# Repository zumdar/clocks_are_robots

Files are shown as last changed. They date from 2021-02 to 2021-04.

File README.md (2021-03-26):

# clocks_are_robots
## ECE3872 musical robot team 5B 

Tinkercad Simulation of Arduino and circuity: <br>
https://www.tinkercad.com/things/kZ8lBtSx1vj-copy-of-ece3872-time-zeeper/editel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

**Arduino Pinouts**

A0 - Audio in <br>
A1 - Enveloped audio in<br>
A2 - Octave knob <br>
<br><br>
[D4 - D7] are for stepper motor<br>
D4 - AIn1<br>
D5 - Ain2<br>
D6 - Bin1<br>
D7 - Bin2<br>
D8 - Start/Stop Button<br>
D9 - Tone out <br>
D10 - Servo out<br>
D12 - Neopixel LED out<br>

# glamour shots

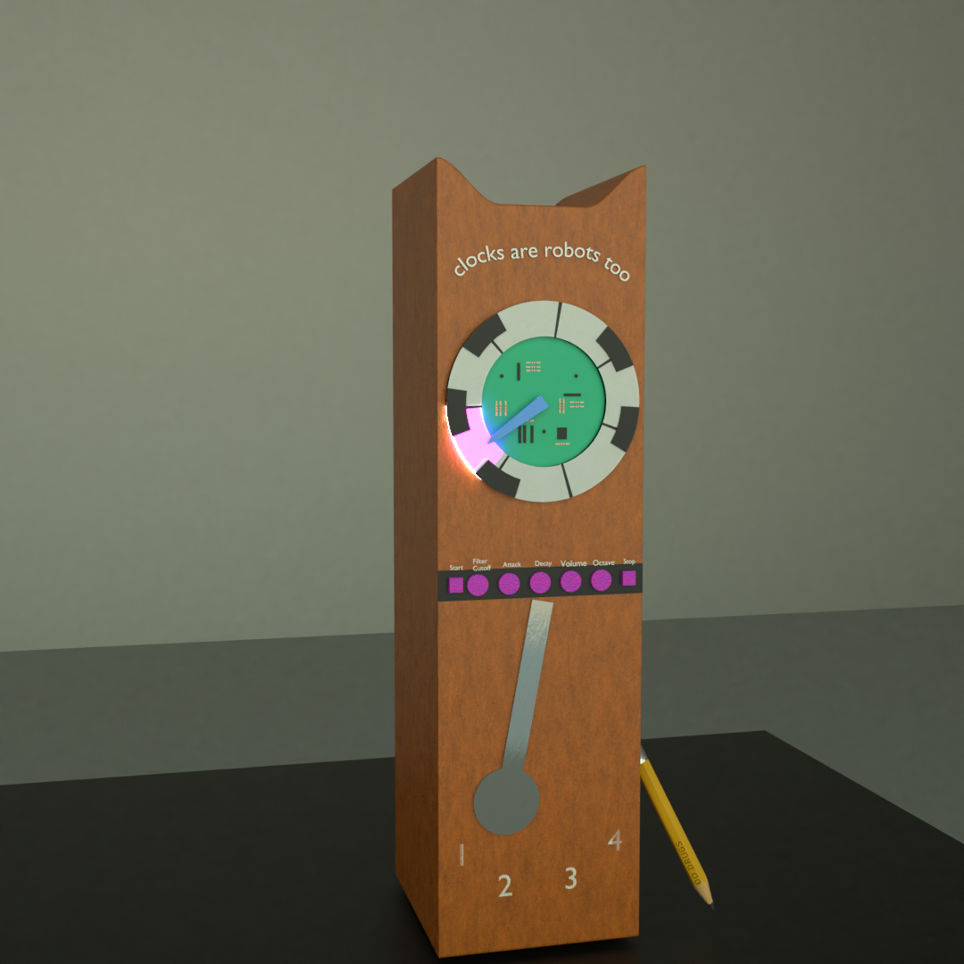
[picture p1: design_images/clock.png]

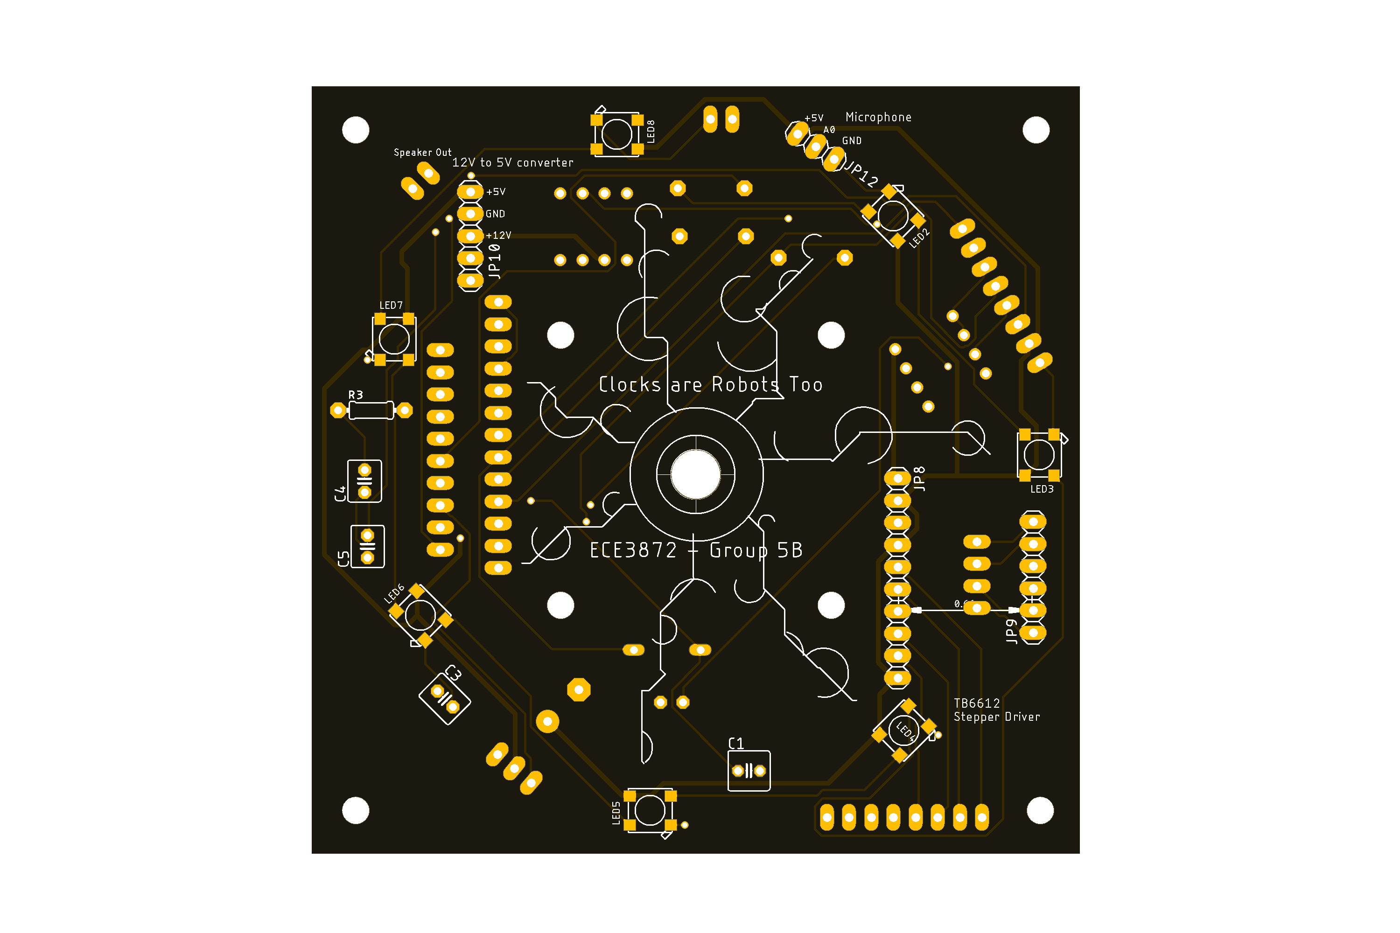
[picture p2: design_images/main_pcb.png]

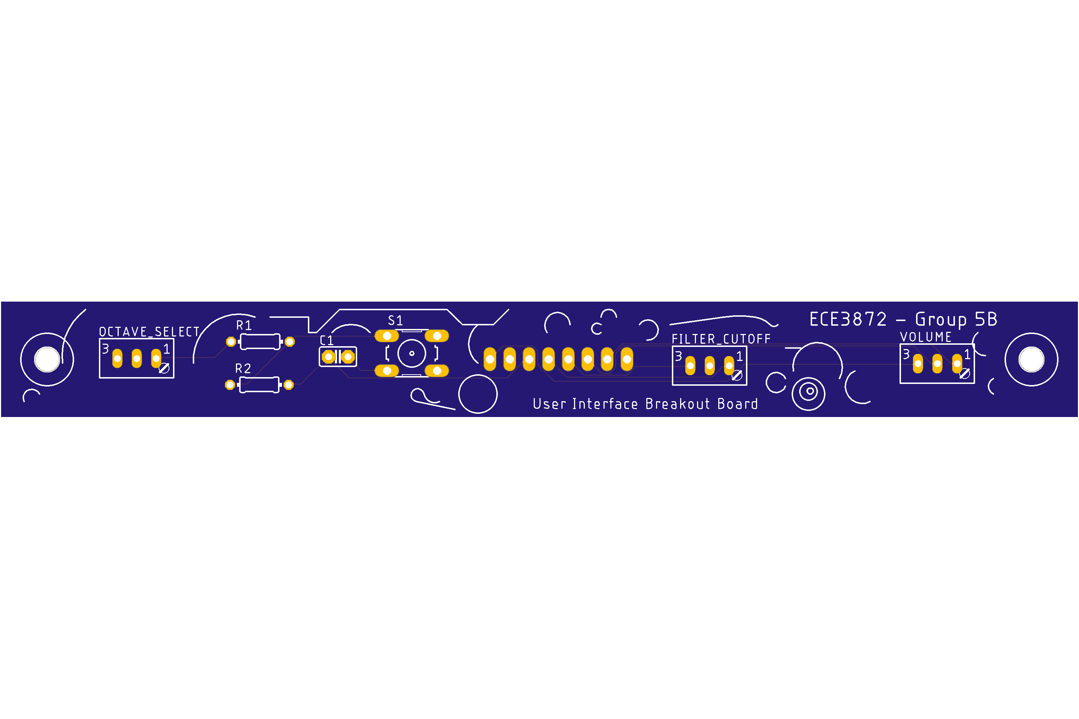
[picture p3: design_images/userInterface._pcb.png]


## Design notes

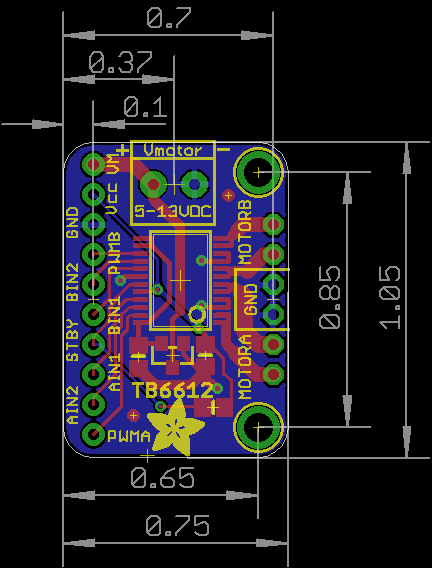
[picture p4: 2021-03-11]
schematics and PCBs/Main_Schematic_and_PCB/StepperMotorDriver_footprint.png

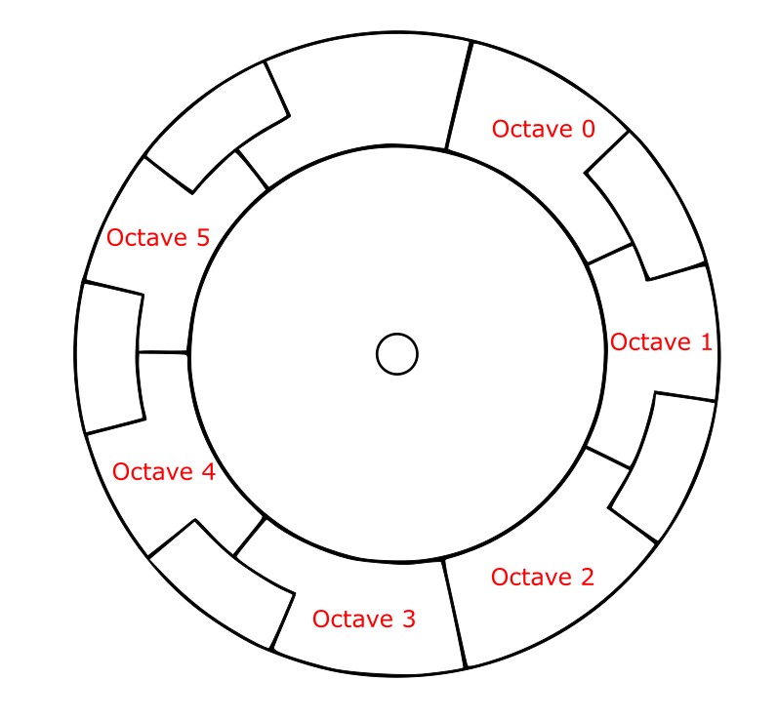
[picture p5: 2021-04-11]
physical_design_files/Annotation 2021-04-11 151619.jpg

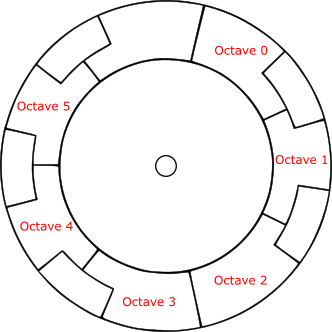
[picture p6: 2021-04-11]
physical_design_files/path1035.png

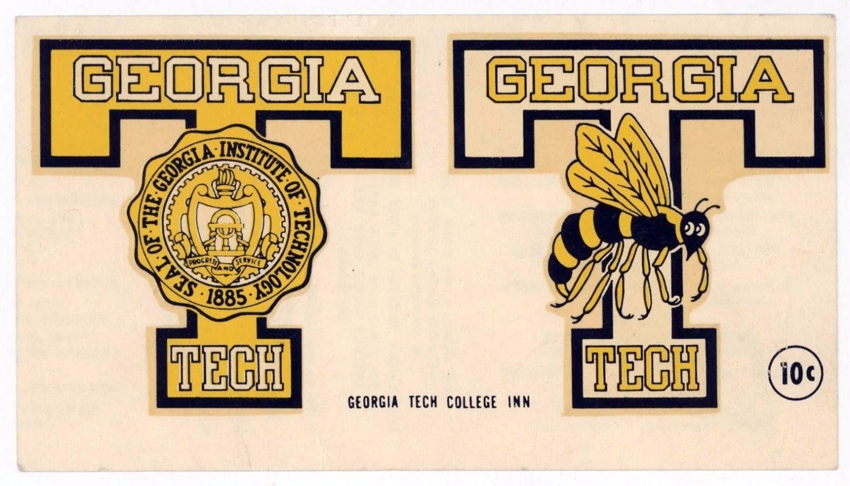
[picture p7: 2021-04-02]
physical_design_files/full clock svgs/f85bab5458ab0abd7dc41fa806446cff.jpg

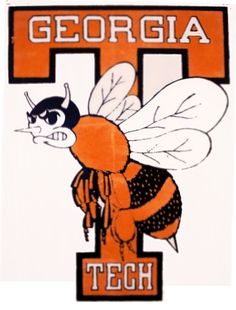
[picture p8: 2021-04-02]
physical_design_files/full clock svgs/cf619c819b96847c2e3a3e8340d46b5b--georgia-decals.jpg

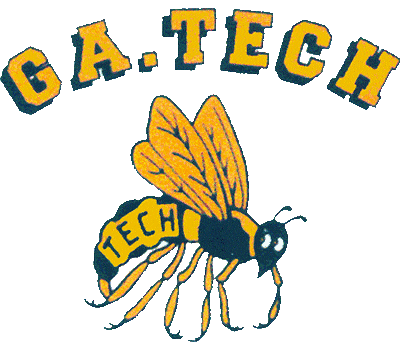
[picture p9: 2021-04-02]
physical_design_files/full clock svgs/d8595733d2d420681d40a56e9d078326.gif

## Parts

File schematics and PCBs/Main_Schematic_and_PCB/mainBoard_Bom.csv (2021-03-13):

Qty | Value | Device | Package | Parts | Description
2 |  | PINHD-1X10 | 1X10 | JP2, JP8 | PIN HEADER
1 |  | PINHD-1X13 | 1X13 | JP1 | PIN HEADER
2 |  | PINHD-1X2 | 1X02 | JP3, JP5 | PIN HEADER
2 |  | PINHD-1X3 | 1X03 | JP7, JP12 | PIN HEADER
1 |  | PINHD-1X4 | 1X04 | JP11 | PIN HEADER
1 |  | PINHD-1X5 | 1X05 | JP10 | PIN HEADER
1 |  | PINHD-1X6 | 1X06 | JP9 | PIN HEADER
2 |  | PINHD-1X8 | 1X08 | JP4, JP6 | PIN HEADER
1 | .05uF | C-US025-040X050 | C025-040X050 | C4 | CAPACITOR, American symbol
1 | 10 | R-US_0204/7 | 0204/7 | R3 | RESISTOR, American symbol
1 | 100 | R-US_0204/7 | 0204/7 | R1 | RESISTOR, American symbol
1 | 1000uF | CPOL-USE5-8.5 | E5-8,5 | C6 | POLARIZED CAPACITOR, American symbol
1 | 100nF | C-US025-040X050 | C025-040X050 | C3 | CAPACITOR, American symbol
1 | 1N4148DO35-7 | 1N4148DO35-7 | DO35-7 | D1 | DIODE
1 | 1k | R-US_0204/7 | 0204/7 | R2 | RESISTOR, American symbol
1 | 1uF | C-US025-040X050 | C025-040X050 | C2 | CAPACITOR, American symbol
1 | 1uF | C-US025-050X050 | C025-050X050 | C1 | CAPACITOR, American symbol
1 | 250uF | C-US025-040X050 | C025-040X050 | C5 | CAPACITOR, American symbol
1 | 470 | R-US_0204/7 | 0204/7 | R4 | RESISTOR, American symbol
1 | LM358N | LM358N | DIL08 | IC2 | OP AMP also LM158; LM258; LM2904
1 | LM386N-1 | LM386N-1 | DIL08 | IC1 | Low Voltage Audio Power Amplifier
7 | WS2812B_5050N | WS2812B_5050N | WS2812B-NARROW | LED2, LED3, LED4, LED5, LED6, LED7, LED8

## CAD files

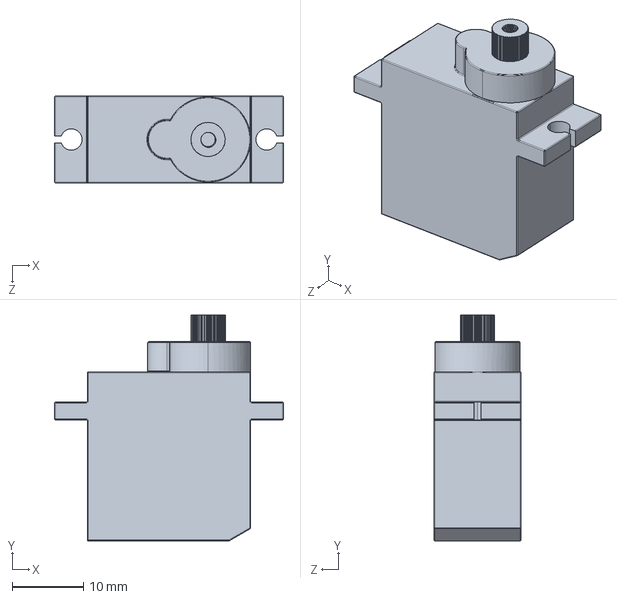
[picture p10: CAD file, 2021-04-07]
physical_design_files/full clock svgs/Servo, Metal Gear, MG90S/Servo, Metal Gear, MG90S.STEP
32.2 x 31.8 x 12.2 mm

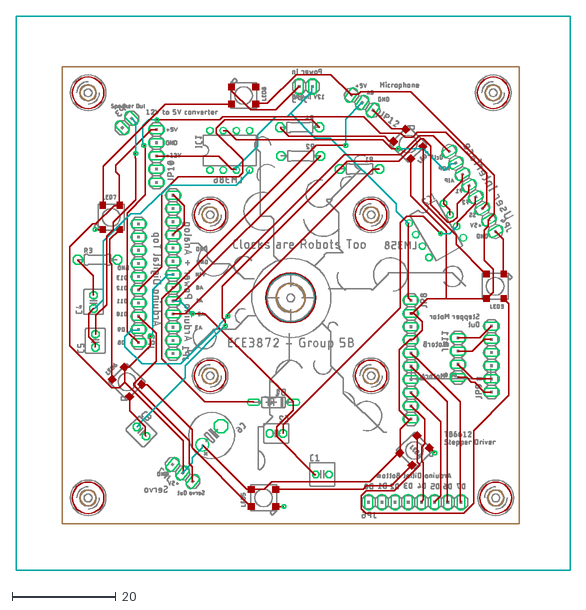
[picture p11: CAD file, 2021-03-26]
schematics and PCBs/Main_Schematic_and_PCB/Finalized Eagle Board Junior Design.dxf
106.7 x 106.7

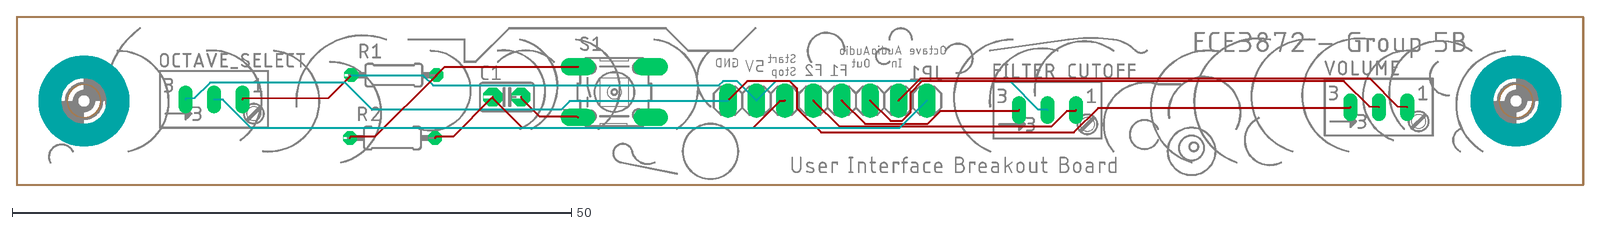
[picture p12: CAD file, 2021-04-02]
schematics and PCBs/userInterface/clockBot_userInterface.dxf
140.2 x 15.2

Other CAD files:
physical_design_files/full clock svgs/Servo, Metal Gear, MG90S/Servo, Metal Gear, MG90S.SLDPRT
physical_design_files/full clock svgs/Servo, Metal Gear, MG90S/Servo, Metal Gear, MG90S.STL

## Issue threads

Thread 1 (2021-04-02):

parts to get

zumdar, 2021-04-02:
switch for power
jack for power
speaker
power supply

zumdar, 2021-04-05:
- [ x ] switch and jack from shop.

zumdar, 2021-04-05:
- [ ] asdas

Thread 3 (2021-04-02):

laser cut TODO

zumdar, 2021-04-02:
make hole mount for servo
add top mounting holes for pcb
add hole for button
holes for pots

zumdar, 2021-04-05:
10.75mm diameter dc in

19.5mm diameter switch w/ 2mm notch on 1 side

zumdar, 2021-04-05:
mg90s servo look for design file online

zumdar, 2021-04-05:
mic mounting hole - 10mm

zumdar, 2021-04-05:
mounting holes for arduino

zumdar, 2021-04-05:
penduluum arm, stepper motor arm

zumdar, 2021-04-07:
get switch cap and measure
make sure filter knob will fit 8mm hole

screws and standoffs
4x M3 - arduino
4x M3 - ext to clock face
2x M3 user interface
2x M3 - voltage converter
standoffs for the clock face

zumdar, 2021-04-07:
- [ ] nuts and washers for pots

zumdar, 2021-04-07:
- [ ] nuts and washer for switch

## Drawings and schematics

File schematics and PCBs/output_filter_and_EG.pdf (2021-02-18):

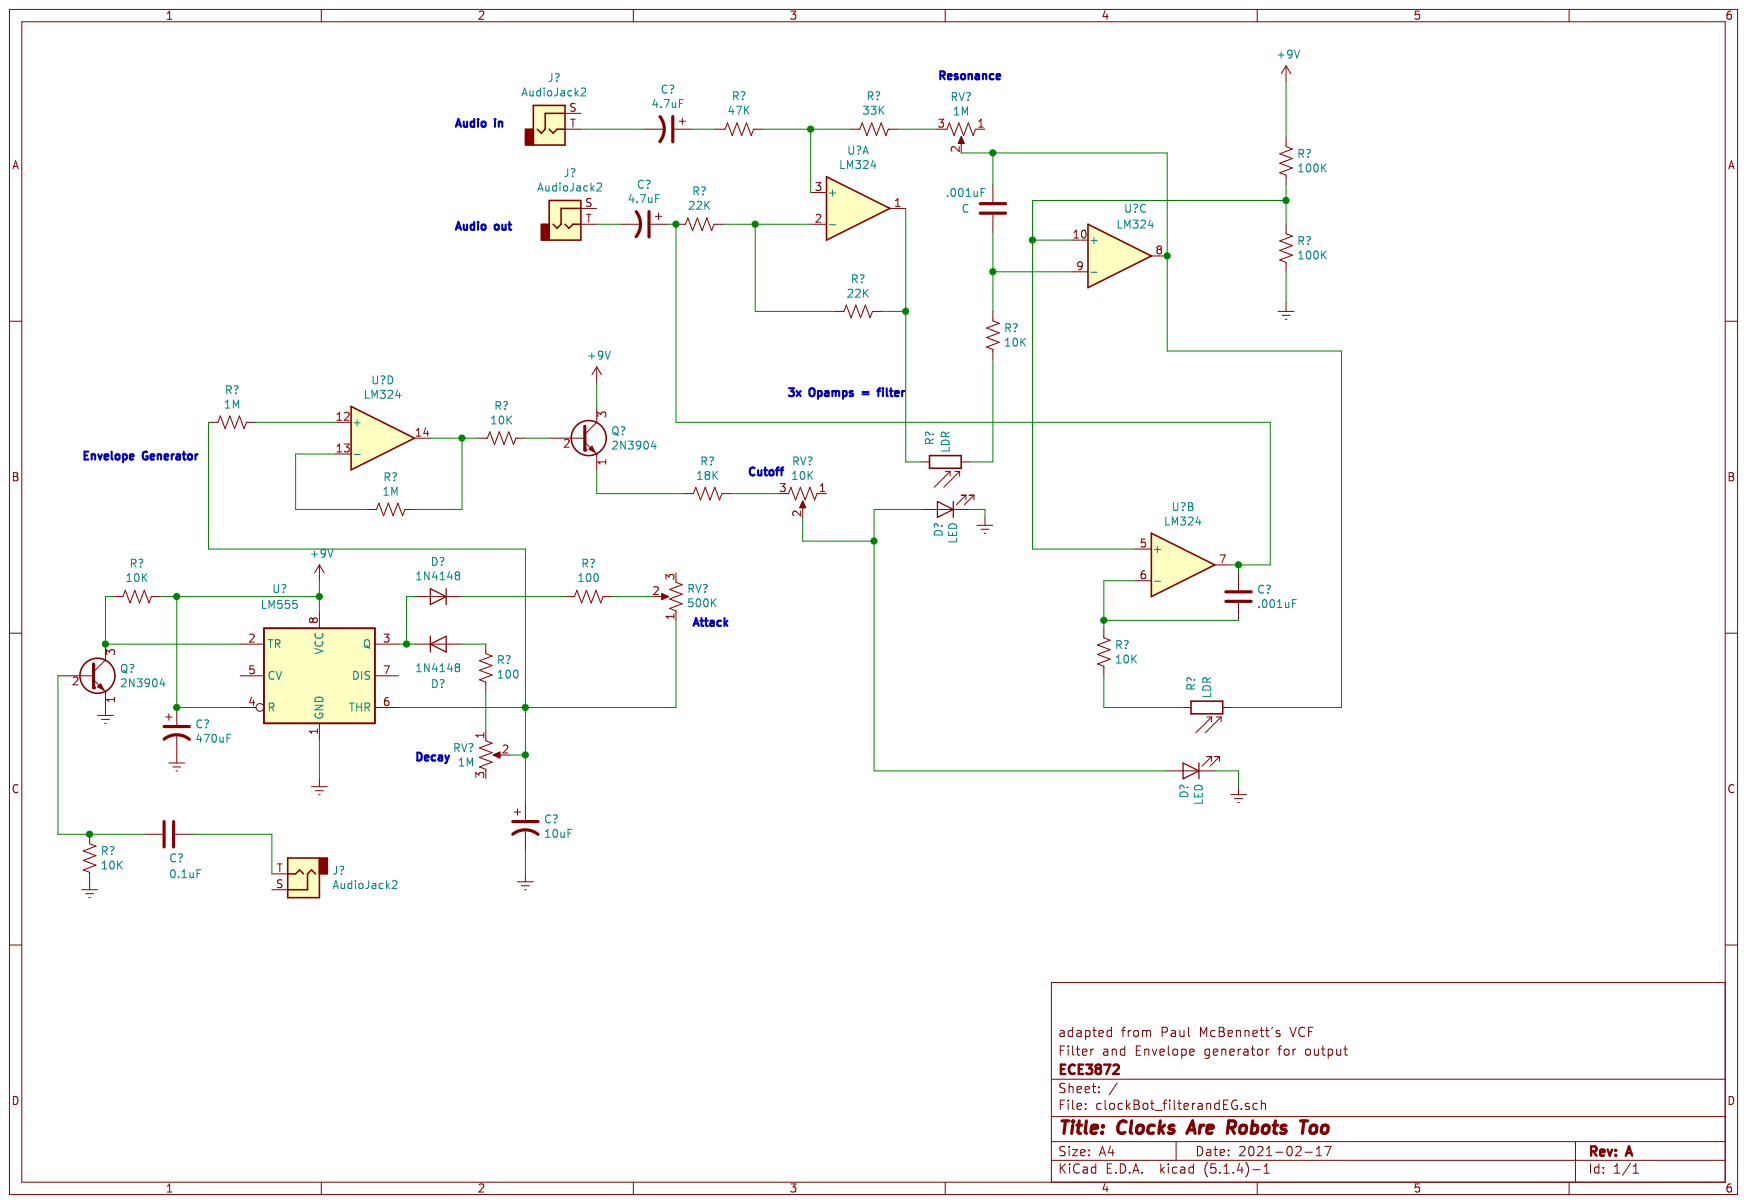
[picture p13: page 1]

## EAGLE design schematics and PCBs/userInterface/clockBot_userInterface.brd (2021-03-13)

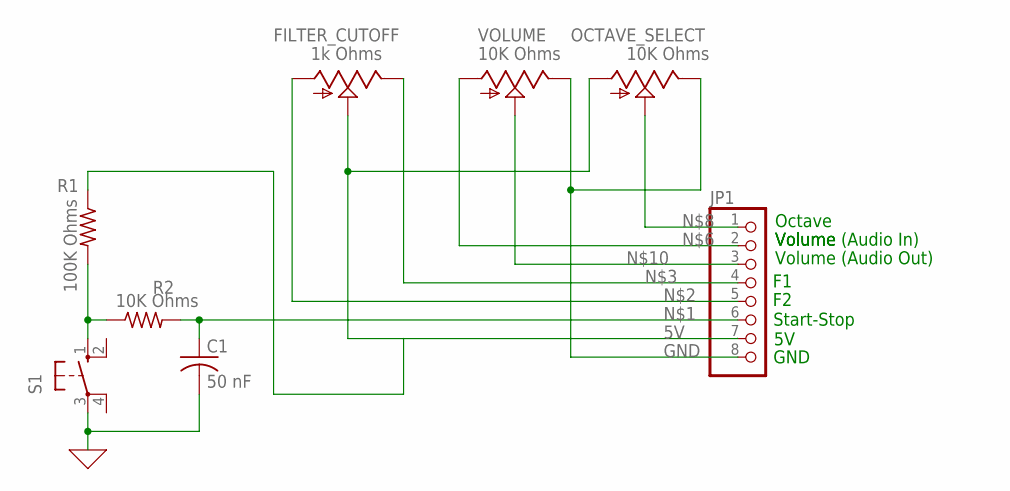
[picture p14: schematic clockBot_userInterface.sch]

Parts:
C1: 50 nF; C025-025X050
FILTER_CUTOFF: 1k Ohms; S64W
JP1: PINHD-1X8; 1X08
OCTAVE_SELECT: 10K Ohms; S64W
R1: 100K Ohms; 0204/7
R2: 10K Ohms; 0204/7
S1: 10-XX; B3F-10XX
VOLUME: 10K Ohms; S64W

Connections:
0: C1.2, S1.3
5V: FILTER_CUTOFF.S, JP1.7, OCTAVE_SELECT.A, R1.1
GND: JP1.8, OCTAVE_SELECT.E, VOLUME.E
unnamed: C1.1, JP1.6, R2.2
unnamed: FILTER_CUTOFF.A, JP1.5
unnamed: FILTER_CUTOFF.E, JP1.4
unnamed: JP1.2, VOLUME.A
unnamed: R1.2, R2.1, S1.1 (S)
unnamed: JP1.1, OCTAVE_SELECT.S
unnamed: JP1.3, VOLUME.S

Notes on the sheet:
Octave
Volume
GND
Start-Stop
Volume (Audio Out)
Volume (Audio In)

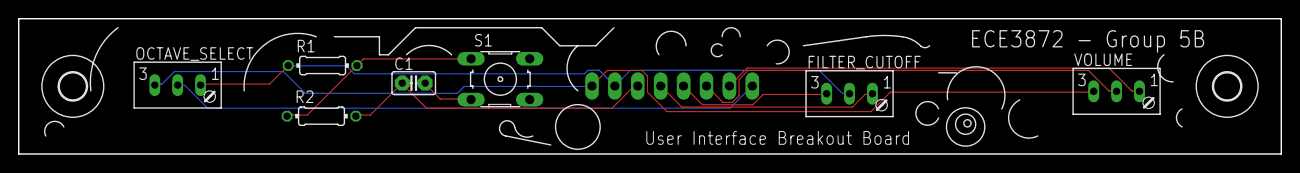
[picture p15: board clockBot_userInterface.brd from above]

Board: 2 copper layers, 140.0 x 15.0 mm, 10 parts (1 on the bottom side), 10 nets.

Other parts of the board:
U$1, U$2: 3,0

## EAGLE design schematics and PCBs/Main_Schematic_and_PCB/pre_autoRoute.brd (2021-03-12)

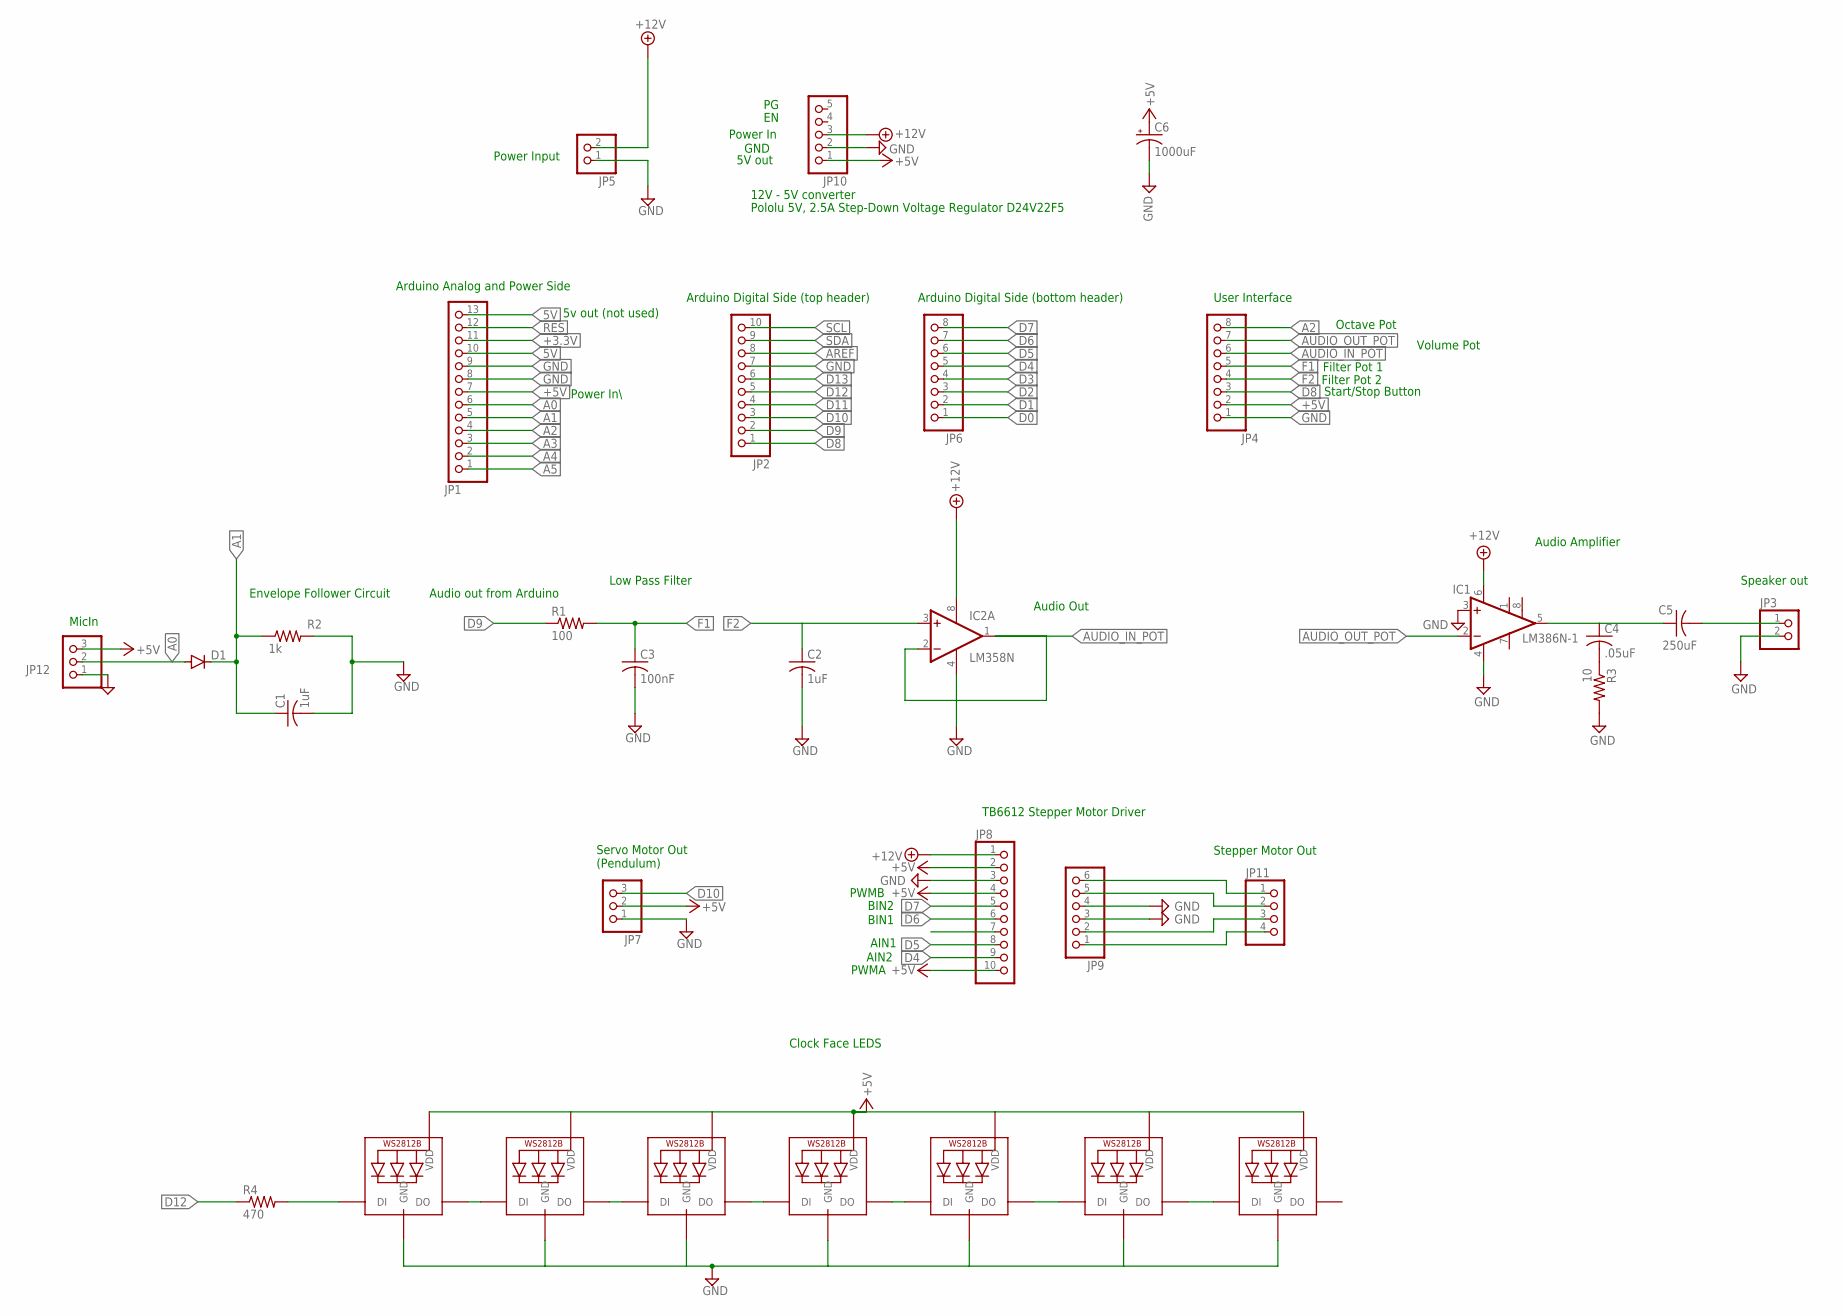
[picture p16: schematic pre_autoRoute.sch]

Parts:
C1: 1uF; C025-050X050
C2: 1uF; C025-040X050
C3: 100nF; C025-040X050
C4: .05uF; C025-040X050
C5: 250uF; C025-040X050
C6: 1000uF; E5-8,5
D1: 1N4148DO35-7; DO35-7
IC1: LM386N-1; DIL08
IC2: LM358N; DIL08
JP1: PINHD-1X13; 1X13
JP2, JP8: PINHD-1X10; 1X10
JP3, JP5: PINHD-1X2; 1X02
JP4, JP6: PINHD-1X8; 1X08
JP7, JP12: PINHD-1X3; 1X03
JP9: PINHD-1X6; 1X06
JP10: PINHD-1X5; 1X05
JP11: PINHD-1X4; 1X04
LED2, LED3, LED4, LED5, LED6, LED7, LED8: WS2812B_5050N; WS2812B-NARROW
R1: 100; 0204/7
R2: 1k; 0204/7
R3: 10; 0204/7
R4: 470; 0204/7

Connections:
5V: JP1.10, JP1.13
+3.3V: JP1.11
+5V: C6.+, JP1.7, JP4.2, JP7.2, JP8.2, JP8.4, JP8.10, JP10.1, JP12.3, LED2.1-VDD (VDD), LED3.1-VDD (VDD), LED4.1-VDD (VDD), LED5.1-VDD (VDD), LED6.1-VDD (VDD), LED7.1-VDD (VDD), LED8.1-VDD (VDD)
+12V: IC1.6 (VS), IC2.8 (V+), JP5.2, JP8.1, JP10.3
A0: D1.A, JP1.6, JP12.2
A1: C1.1, D1.C, JP1.5, R2.1
A2: JP1.4, JP4.8
A3: JP1.3
A4: JP1.2
A5: JP1.1
AREF: JP2.8
AUDIO_IN_POT: IC2.1 (OUT), IC2.2 (-IN), JP4.6
AUDIO_OUT_POT: IC1.2 (-IN), JP4.7
D0: JP6.1
D1: JP6.2
D2: JP6.3
D3: JP6.4
D4: JP6.5, JP8.9
D5: JP6.6, JP8.8
D6: JP6.7, JP8.6
D7: JP6.8, JP8.5
D8: JP2.1, JP4.3
D9: JP2.2, R1.1
D10: JP2.3, JP7.3
D11: JP2.4
D12: JP2.5, R4.1
D13: JP2.6
F1: C3.1, JP4.5, R1.2
F2: C2.1, IC2.3 (+IN), JP4.4
GND: C1.2, C2.2, C3.2, C6.-, IC1.3 (+IN), IC1.4 (GND), IC2.4 (V-), JP1.8, JP1.9, JP2.7, JP3.2, JP4.1, JP5.1, JP7.1, JP8.3, JP9.3, JP9.4, JP10.2, JP12.1, LED2.3-GND (GND), LED3.3-GND (GND), LED4.3-GND (GND), LED5.3-GND (GND), LED6.3-GND (GND), LED7.3-GND (GND), LED8.3-GND (GND), R2.2, R3.2
unnamed: C4.2, R3.1
unnamed: LED2.4-DIN (DI), R4.2
unnamed: C4.1, C5.1, IC1.5 (OUT)
unnamed: C5.2, JP3.1
unnamed: LED2.2-DOUT (DO), LED3.4-DIN (DI)
unnamed: LED4.2-DOUT (DO), LED5.4-DIN (DI)
unnamed: LED5.2-DOUT (DO), LED6.4-DIN (DI)
unnamed: LED6.2-DOUT (DO), LED7.4-DIN (DI)
unnamed: LED7.2-DOUT (DO), LED8.4-DIN (DI)
unnamed: LED3.2-DOUT (DO), LED4.4-DIN (DI)
unnamed: JP9.6, JP11.1
unnamed: JP9.5, JP11.2
unnamed: JP9.2, JP11.3
unnamed: JP9.1, JP11.4
RES: JP1.12
SCL: JP2.10
SDA: JP2.9

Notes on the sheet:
Envelope Follower Circuit
MicIn
Audio Out
Power Input
Low Pass Filter
Power In
GND
5V out
12V - 5V converter
Pololu 5V, 2.5A Step-Down Voltage Regulator D24V22F5
Power In\
5v out (not used)
Arduino Analog and Power Side
Octave Pot
Volume Pot
Filter Pot 1
Filter Pot 2
Start/Stop Button
Speaker out
User Interface
Servo Motor Out (Pendulum)
Clock Face LEDS
Arduino Digital Side (bottom header)
Arduino Digital Side (top header)
PWMA
PWMB
AIN1
AIN2
BIN1
BIN2
TB6612 Stepper Motor Driver
Stepper Motor Out
Audio out from Arduino
Audio Amplifier

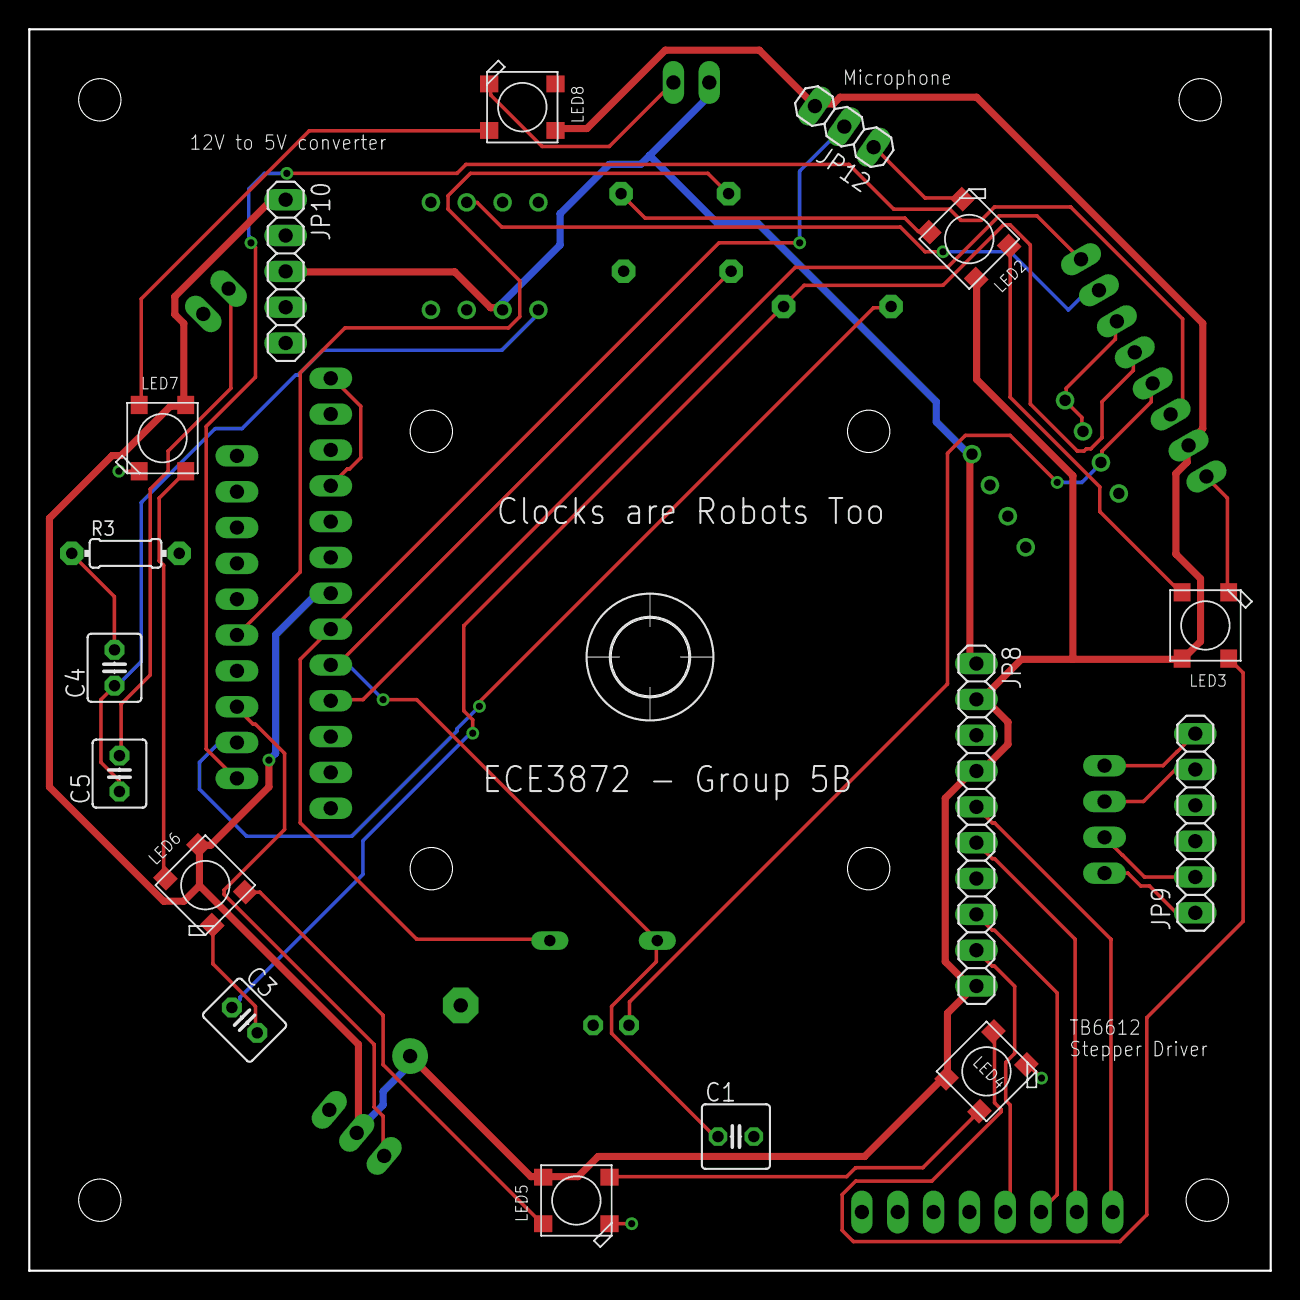
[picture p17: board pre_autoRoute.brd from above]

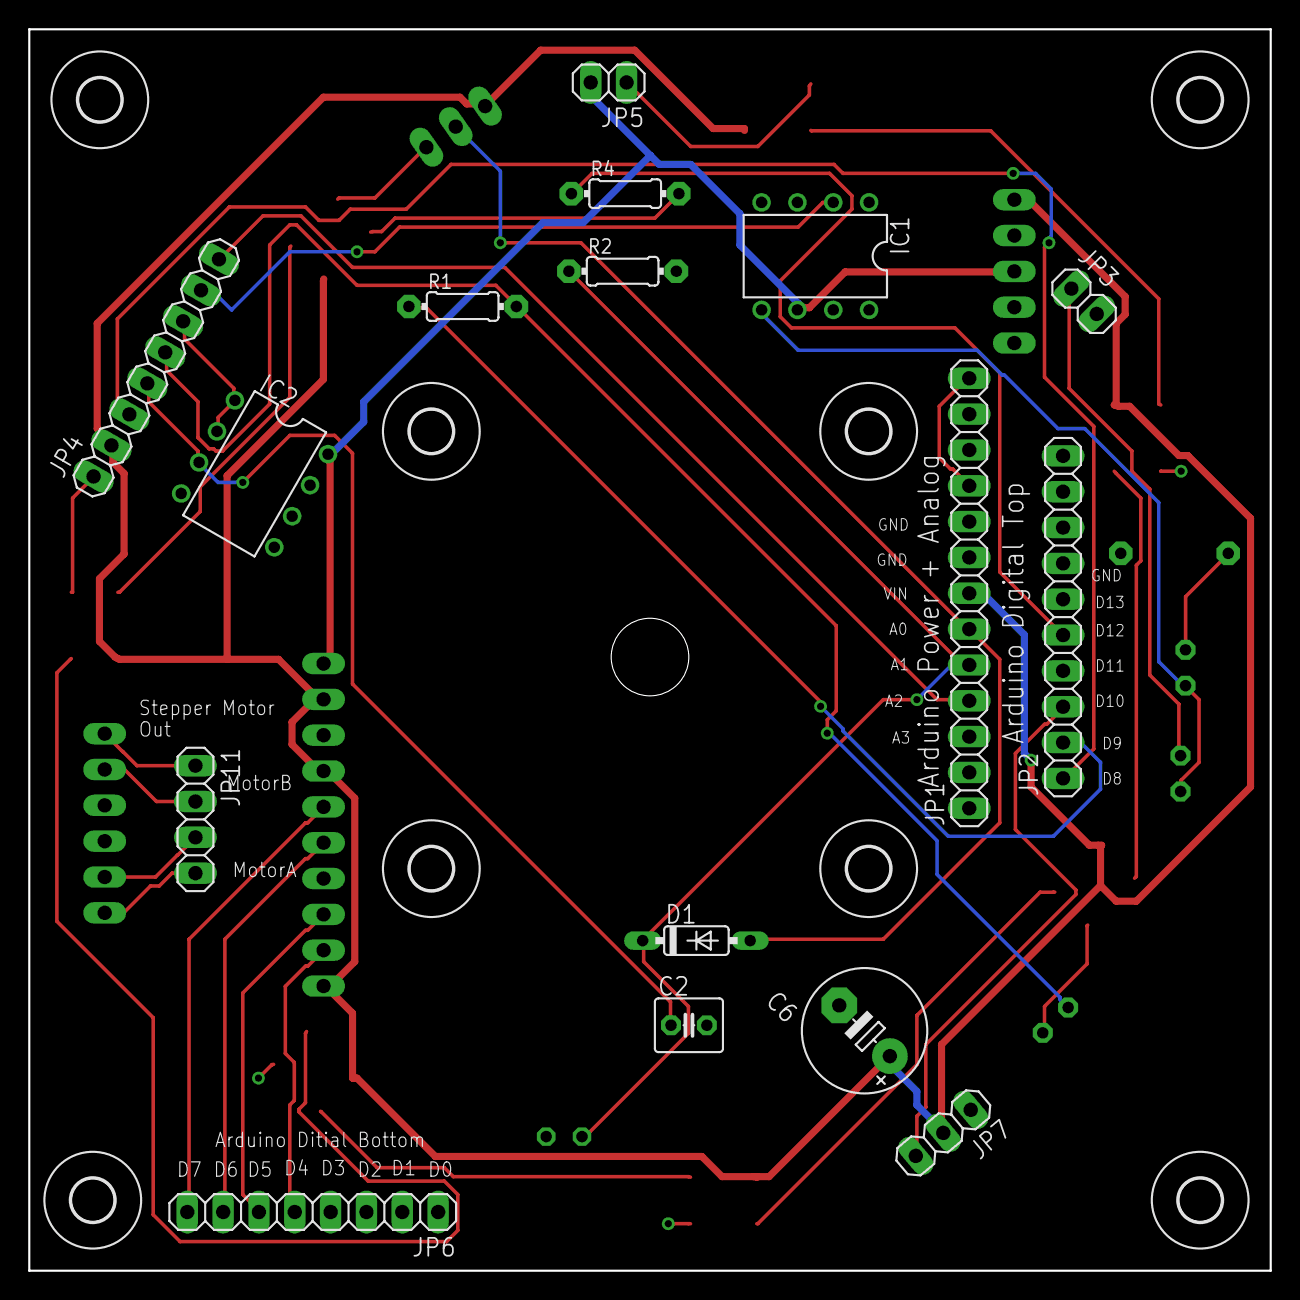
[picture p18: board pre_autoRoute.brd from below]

Board: 2 copper layers, 88.0 x 88.0 mm, 41 parts (24 on the bottom side), 33 nets.

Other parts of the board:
U$1: 5,5
U$2, U$3, U$4, U$5, U$6, U$7, U$8, U$9: 3,0

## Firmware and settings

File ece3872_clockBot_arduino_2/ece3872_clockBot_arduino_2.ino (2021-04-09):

//-----------------------------------------------------
// Engineer: William Kennedy, Alex Liu, Erin-Grace Walden, Solomon Martin
// Overview:
//    When this device is turned on it listens to the conductor play
//    plays a song with the conductor. It also displays
//    what pitches it is playing with a servo and leds
//    and displays the timing with a metronome like penduluum
// Design Name:   clocks are robots too
// File Name:     roboclock.ino
//
// Inputs:
//    Start Switch: switch to start playing the song
//    Stop switch: stops the song
//    Volume: controls the volume
//    Tempo: controls the tempo of the song
//    Octave Select: control the octave of the song
// Outputs:
//    Speaker: Used to play the song
//
//
// History:       4 February 2021 - William - File created
//                1 March 2021 - Solomon - Tempo and Windowing Functionality Added
//
//-----------------------------------------------------

// TODO: create array for servo positions based on note (similar to the notes array)
//create lighting array
// TODO: integrate stepper motor w/ main code
// create pendluluum rotation based on tempo
// put in code for buttons
// put in code for octave switching

#include <Servo.h>
#include <Adafruit_NeoPixel.h>
#include <stdio.h>
#include <math.h>
#include <Stepper.h>




// OUTPUT SETUP (servos, leds, speaker)
#define LED_PIN 12
#define LED_COUNT 7
#define BRIGHTNESS 255
#define SPEAKER_PIN 9
//#define TEST_INPUT 6

Adafruit_NeoPixel strip(LED_COUNT, LED_PIN, NEO_GRB + NEO_KHZ800); // Declare NeoPixel strip object:
Servo metronomeServo;  // create servo object to control a metronom servo

//INPUT SETUP
int octavePin = A2;
int tempoPin = A1; // envelope or comparator input
int audioInput = A0;
#define threshold 200 // Conventions are bad, this is only temporary. Replace w/ threshold input
#define START_BUTTON 8

//SOUND SETUP
#define TempoCal 512
#define TempoPotMax 1023
#define PwmMax 255
int octave = 4; //Default 4 but should change

//Music Notes based on Octave--
float C = 16.3516*pow(2,octave);
float D = 18.35405*pow(2,octave);
float E = 20.60172*pow(2,octave);
float F = 21.82676*pow(2,octave);
float G = 24.49971*pow(2,octave);
float A = 27.5*pow(2,octave);
float B = 30.86771*pow(2,octave);
float high_C = 32.70320*pow(2,octave);
float rest = 0;

// servo rotations based on notes
#define Cserv 0
#define Dserv 29
#define Eserv 57
#define Fserv 86
#define Gserv 114
#define Aserv 143
#define Bserv 171
#define high_Cserv 200

// led index based on notes
#define Cled 0
#define Dled 1
#define Eled 2
#define Fled 3
#define Gled 4
#define Aled 5
#define Bled 6
#define high_Cled 0

// led color based on notes

uint32_t Ccolor = strip.ColorHSV(0);
uint32_t Dcolor = strip.ColorHSV(9362);
uint32_t Ecolor = strip.ColorHSV(18725);
uint32_t Fcolor = strip.ColorHSV(28087);
uint32_t Gcolor = strip.ColorHSV(37449);
uint32_t Acolor = strip.ColorHSV(46811);
uint32_t Bcolor = strip.ColorHSV(56174);
uint32_t high_Ccolor = strip.ColorHSV(65534);


// playOutput Globals
bool startSong = 0;
bool skipProcessing = 0;
bool testOutput = 0;
bool music = 1;
bool lights = 1;
bool motors = 1;

int pitchPos = 0;    // variable to store the pitch servo position
int metronomePos = 0;    // variable to store the metronome penduluum servo position
int metronomePosMapped;
double tempo;

//Row Row Row Your Boat
int songLength = 54;
//double notes[] = {C, rest, C, rest, C, rest, D, rest, E, rest, E, rest, D, rest, E, rest, F, rest, G, rest, high_C, rest, high_C, rest, high_C, rest, G, rest, G, rest, G, rest, E, rest, E, rest, E, rest, C, rest, C, rest, C, rest, G, rest, F, rest, E, rest, D, rest, C, rest};
float* notes[] = {&C, &rest, &C, &rest, &C, &rest, &D, &rest, &E, &rest, &E, &rest, &D, &rest, &E, &rest, &F, &rest, &G, &rest, &high_C, &rest, &high_C, &rest, &high_C, &rest, &G, &rest, &G, &rest, &G, &rest, &E, &rest, &E, &rest, &E, &rest, &C, &rest, &C, &rest, &C, &rest, &G, &rest, &F, &rest, &E, &rest, &D, &rest, &C, &rest};
int beats[] = {2, 1, 2, 1, 2, 1, 1, 1, 2, 1, 2, 1, 1, 1, 2, 1, 1, 1, 6, 1, 1, 1, 1, 1, 1, 1, 1, 1, 1, 1, 1, 1, 1, 1, 1, 1, 1, 1, 1, 1, 1, 1, 1, 1, 2, 1, 1, 1, 2, 1, 1, 1, 5, 1};

//int songLength = 28;
//int notes[] = {C, C, C, D, E, E, D, E, F, G, high_C, high_C, high_C, G, G, G, E, E, E, C, C, C, G, F, E, D, C, rest};
//int beats[] = {3,3,2,1,3,2,1,2,1,6,1,1,1,1,1,1,1,1,1,1,1,1,2,1,2,1,5,1};
int song_tempo = 250;

int servoNotes[] = {Cserv, Cserv, Cserv, Cserv, Cserv, Cserv, Dserv, Dserv, Eserv, Eserv, Eserv, Eserv, Dserv, Dserv, Eserv, Eserv, Fserv, Fserv, Gserv, Gserv, high_Cserv, high_Cserv, high_Cserv, high_Cserv, high_Cserv, high_Cserv, Gserv, Gserv, Gserv, Gserv, Gserv, Gserv, Eserv, Eserv, Eserv, Eserv, Eserv, Eserv, Cserv, Cserv, Cserv, Cserv, Cserv, Cserv, Gserv, Gserv, Fserv, Fserv, Eserv, Eserv, Dserv, Dserv, Cserv, Cserv};
int ledIndexes[] = {Cled, Cled, Cled, Cled, Cled, Cled, Dled, Dled, Eled, Eled, Eled, Eled, Dled, Dled, Eled, Eled, Fled, Fled, Gled, Gled, high_Cled, high_Cled, high_Cled, high_Cled, high_Cled, high_Cled, Gled, Gled, Gled, Gled, Gled, Gled, Eled, Eled, Eled, Eled, Eled, Eled, Cled, Cled, Cled, Cled, Cled, Cled, Gled, Gled, Fled, Fled, Eled, Eled, Dled, Dled, Cled, Cled};
uint32_t ledColors[] = {Ccolor, Ccolor, Ccolor, Ccolor, Ccolor, Ccolor, Dcolor, Dcolor, Ecolor, Ecolor, Ecolor, Ecolor, Dcolor, Dcolor, Ecolor, Ecolor, Fcolor, Fcolor, Gcolor, Gcolor, high_Ccolor, high_Ccolor, high_Ccolor, high_Ccolor, high_Ccolor, high_Ccolor, Gcolor, Gcolor, Gcolor, Gcolor, Gcolor, Gcolor, Ecolor, Ecolor, Ecolor, Ecolor, Ecolor, Ecolor, Ccolor, Ccolor, Ccolor, Ccolor, Ccolor, Ccolor, Gcolor, Gcolor, Fcolor, Fcolor, Ecolor, Ecolor, Dcolor, Dcolor, Ccolor, Ccolor};

//Test mode
int mode = LOW;
int modeSecond = LOW;

//Function Prototypes
void buttonISR(int);
double getTempo(float);
int* DFTind(int, float);
void solidColor(uint32_t);
void playOutput(void);

//Stepper Motor
int degree = 1.8;
int currAngle = 0;
Stepper myStepper(200, 4, 5, 6, 7);

void setup() {
  myStepper.setSpeed(60);
  pinMode(octavePin, INPUT);
  pinMode(tempoPin, INPUT);
  pinMode(audioInput, INPUT);
  pinMode(START_BUTTON, INPUT);
  pinMode(SPEAKER_PIN, OUTPUT);
  
  metronomeServo.attach(10);

  strip.begin();           // INITIALIZE NeoPixel strip object (REQUIRED)
  strip.show();            // Turn OFF all pixels ASAP
  strip.setBrightness(BRIGHTNESS);

  //debug only
  Serial.begin(9600);
  Serial.print("Setup Complete\n");
}

void loop() {

  while (true) { // Do not continue until we see a button press
    Serial.println("Waiting for button press");
    solidColor(strip.ColorHSV(56000, 255,   255)); // Green
    mode = !digitalRead(START_BUTTON);
    if (mode == HIGH) {
      long buttonPressStart = millis();
      while (millis() - buttonPressStart < 3000) {}; // Functionally the same as delay(3000), but we could define some actions within loop if necessesary
      modeSecond = !digitalRead(START_BUTTON);
      break;
    }
  }

  if (mode == HIGH && modeSecond == HIGH) {
    // test mode
    Serial.println("Test mode");
    mode = LOW;
    modeSecond = LOW;

    while (true) { // Do not continue until we see a button press
      Serial.println("Waiting for input/output");
      solidColor(strip.ColorHSV(10922, 255,   255));
      mode = !digitalRead(START_BUTTON);
      if (mode == HIGH) {
        long buttonPressStart = millis();
        while (millis() - buttonPressStart < 3000) {}; // Functionally the same as delay(3000), but we could define some actions within loop if necessesary
        modeSecond = !digitalRead(START_BUTTON);
        break;
      }
    }
    if (mode == HIGH && modeSecond == HIGH) {
      //Output Test
      Serial.println("Output Test");
      ///----------------------------------
      ///TEST PROCEDURE FOR LEDS AND SERVOS
      //------------------------------------
      solidColor(strip.ColorHSV(32000,   255,   255)); // Red
      delay(200);
      solidColor(strip.ColorHSV(56000, 255,   255)); // Green
      delay(200);
      solidColor(strip.ColorHSV(10000,   255, 255)); // Blue
      delay(200);
      tempo = 0.125; // Hardcoded tempo for
      startSong = 1;
      playOutput();
      for (int angle : servoNotes) {
        int difference = angle - currAngle;
        Serial.println("clockwise");
        myStepper.step(difference / degree);
        delay(50);
        currAngle = angle;
      }
    } else if (mode == HIGH && modeSecond == LOW) {
      Serial.println("Input Test");
      long startInputTest = millis();
      int brightness;
      while (true) {
        if (!digitalRead(START_BUTTON)) {
          break;
        }
        strip.clear();
        brightness = round((analogRead(tempoPin) - 360)*255.0/20.0);
        strip.setPixelColor(0, brightness);
        strip.setPixelColor(1, brightness);
        strip.setPixelColor(2, brightness);
        strip.setPixelColor(3, brightness);
        strip.setPixelColor(4, brightness);
        strip.setPixelColor(5, brightness);
        strip.setPixelColor(6, brightness);
        strip.setPixelColor(7, brightness);
        strip.setPixelColor(8, brightness);
        strip.show();
        Serial.println(analogRead(tempoPin));
        while(millis() - startInputTest < 500) {};
      }
    }
  } else if (mode == HIGH && modeSecond == LOW) {
    // normal play mode
    Serial.println("Play mode");
    while (digitalRead(START_BUTTON)) { // Loop until next press
      Serial.println("Waiting for octave select.");
      myStepper.step(5);
      octave = 1024 - analogRead(octavePin); //TODO: Map 1024 input values to 6 discrete octave values (0-5 for now)
      if (octave >= 0 && octave < 170) {
        strip.clear();
        strip.setPixelColor(0, Ccolor);
        strip.show();
        octave = 0;
      } else if (octave >= 170 && octave < 340) {
        strip.clear();
        strip.setPixelColor(1, Ccolor);
        strip.show();
        octave = 1;
      } else if (octave >= 340 && octave < 510) {
        strip.clear();
        strip.setPixelColor(2, Ccolor);
        strip.show();
        octave = 2;
      } else if (octave >= 510 && octave < 680) {
        strip.clear();
        strip.setPixelColor(3, Ccolor);
        strip.show();
        octave = 3;
      } else if (octave >= 680 && octave < 850) {
        strip.clear();
        strip.setPixelColor(4, Ccolor);
        strip.show();
        octave = 4;
      } else if (octave >= 850 && octave <= 1024) {
        strip.clear();
        strip.setPixelColor(5, Ccolor);
        strip.show();
        octave = 5;
      }
      Serial.println(octave);
    }
    if (octave == 1) {
        int difference = Cserv - Dserv;
        myStepper.step(difference/degree);
      } else if (octave == 2) {
        int difference = Cserv - Eserv;
        myStepper.step(difference/degree);
      } else if (octave == 3) {
        int difference = Cserv - Fserv;
        myStepper.step(difference/degree);
      } else if (octave == 4) {
        int difference = Cserv - Gserv;
        myStepper.step(difference/degree);
      } else if (octave == 5) {
        int difference = Cserv - Aserv;
        myStepper.step(difference/degree);
      }
    currAngle = 0;
    redefineNotes();
    strip.clear();

    //play mode
    int tempoRaw;
    int sampleRate = 2500; // Limits highest input octave to 5, by nyquist sampling of high_C
    int motor_speed;
    ///----------------------------------
    ///TEMPO DETECTION & DELAY SYNC
    //------------------------------------

    tempo = getTempo(1.0 / sampleRate);
    int DFTsize = 256; //Hopefully multiple of two helps speed
    int* FFTindices = DFTind(DFTsize, 1.0 / sampleRate);
    int windowLength = 256;
    int window[windowLength];
    float v[8][3];
    float fftValues[8];
    int strongFreq[6] = {0, 0, 0, 0, 0, 0}; // We want [E, *, D, *, C, C];

    bool detected = false;
    unsigned long currTime;
    int cnt = 0;

    int state = 0; //E is 3, D is 2, C is 1
    int input; // Input to state machine

    while (!detected && !skipProcessing) {
      if (digitalRead(START_BUTTON)) {
        buttonISR(1);
      }
      for (int i = 0; i < windowLength; i++) {
        currTime = micros();
        window[i] = analogRead(audioInput); // collect window
        while (micros() - currTime < long(1000000.0 / sampleRate)) {} // delay by sample period
      }

      // Goertzel calculation of FFT values
      for (int* k = FFTindices; k < FFTindices + 4; k++) {
        int f = k - FFTindices; //index based on frequency
        for (int n = 0; n < DFTsize; n++) {
          if (n == 0) {
            v[f][2] = window[0];
          } else if (n == 1) {
            v[f][1] = v[f][2];
            v[f][2] = 2 * cos(2.0 * 3.14 * (*k) / DFTsize) * v[f][1] + window[1];
          } else {
            v[f][0] = v[f][1];
            v[f][1] = v[f][2];
            v[f][2] = 2 * cos(2.0 * 3.14 * (*k) / DFTsize) * v[f][1] - v[f][0] + window[n];
          }
        }
        fftValues[f] = pow(v[f][2], 2) + pow(v[f][1], 2) - 2 * cos(-2.0 * 3.14 * (*k) / DFTsize) * v[f][2] * v[f][1];
      }

      // Associate the most recent window w/ a note given frequency values
      for (int i = 1; i < sizeof(strongFreq) / sizeof(int); i++) { //shifting previous values back
        strongFreq[i - 1] = strongFreq[i];
      }
      // Determine strongest frequency
      float maximum = fftValues[0]; //Initializing max at first value
      int maxInd = 0;
      for (int i = 1; i < 4; i++) {
        if (fftValues[i] > maximum) {
          maximum = fftValues[i];
          maxInd = i;
        }
      }

      // State Machine Implementation for Pattern Detection
      input = strongFreq[sizeof(strongFreq) / sizeof(int) - 1]; //most recent value
      if (state == 0) { //start
        if (input == 3) {
          state = 1;
        }
      } else if (state == 1) { // E
        if (input == 1) {
          state = 2;
        } else if (input == 3) {
          // stay at E
        } else {
          state = 0; // Back to start
        }
      } else if (state == 2) { // First Rest
        if (input == 2) {
          state = 3;
        } else if (input == 1) {
          // stay at rest
        } else {
          state = 0; //reset
        }
      } else if (state == 3) { // D
        if (input == 1) {
          state = 4;
        } else if (input == 2) {
          // stay at D
        } else {
          state = 0; //reset
        }
      } else if (state == 4) { // Second Rest
        detected = true;
      }

    }

    if (skipProcessing) { //Skip determined by buttonISR in either of the tempo detection and time sync loops
      if (startSong) {
        strip.clear();
        strip.setPixelColor(0, 255, 0, 255);
        strip.show();
        while (!digitalRead(START_BUTTON)) {}; //Show status lights and then play on next press
        playOutput();
      }
      skipProcessing = false;
      return; //Go back to init state
    }

    while (analogRead(tempoPin) > threshold) { } //let C finish
    //  Serial.println("Waiting for C to finish");
    while (analogRead(tempoPin) < threshold) { } //let rest finish
    //  Serial.println("Final rest finished, now PLAY!!");
    // while (true) {
    //   Serial.println(analogRead(audioInput));
    // }
    //TODO: Verify playing on time w/ speaker
    //------------------------------------
    //playing THE SONG
    //------------------------------------

    startSong = 1;
    while (true)
    {
      if (!startSong) {
        break;
      } else {
        playOutput();
      }
    }

  }
}

void buttonISR(int code = 0) { // Not really an ISR. Saving commented code for more complex test routines
  if (code == 0) {
    startSong = 0;
  } else if (code == 1) {
    skipProcessing = true;
    long startPress = millis();
    while (digitalRead(START_BUTTON)) {}
    if (millis() - START_BUTTON >= 3000) {
      startSong = true;
    }
  }
  // long currTime = millis();
  // int riseCount = 0;
  // int currLevel = 0;
  // int pastLevel = digitalRead(START_BUTTON);
  // while (millis() - currTime < 20) { // detect # of rising edges over 20 ms
  //   currLevel = digitalRead(START_BUTTON);
  //   if (currLevel && !pastLevel) {
  //     riseCount++;
  //   }
  //   pastLevel = currLevel;
  // }
  // switch (riseCount) { //TODO take another look at the redundancy by startSong and testOutput
  // case 0: // Play song in loop
  //   music = 1;
  //   lights = 1;
  //   motors = 1;
  //   startSong = 1;
  //   testOutput = 0;
  //   break;
  // case 1: // All test
  //   music = 1;
  //   lights = 1;
  //   motors = 1;
  //   startSong = 0;
  //   testOutput = 1;
  //   break;
  // case 2:
  //   music = 1;
  //   lights = 0;
  //   motors = 0;
  //   startSong = 0;
  //   testOutput = 1;
  //   break;
  // case 3:
  //   music = 0;
  //   lights = 1;
  //   motors = 0;
  //   startSong = 0;
  //   testOutput = 1;
  //   break;
  // case 4:
  //   music = 0;
  //   lights = 0;
  //   motors = 1;
  //   startSong = 0;
  //   testOutput = 1;
  //   break;
  // }
}


void solidColor(uint32_t color) {
  for (int i = 0; i < strip.numPixels(); i++) {
    strip.setPixelColor(i, color);         //  Set pixel's color (in RAM)
  }
  strip.show(); // must call this everytime you want the LEDs to update
}

void playOutput() {

  unsigned int mic = 0;
  int i_note_index = 0;
  int duration;
  long metronomeTimer;
  int metronomeMovement = 0;

  while (i_note_index < songLength) {
    if (!digitalRead(START_BUTTON)) {
      buttonISR(0);
    }
    if (!startSong) {
      break;
    }

    Serial.println(tempo);


    mic = analogRead(audioInput);
    Serial.println(mic);

    //play the song
    duration = beats[i_note_index] * tempo * 1000; // in ms
    if (music) {
      tone(SPEAKER_PIN, *notes[i_note_index]*2, duration); // TODO: define w/ Team what octave we should play in
    }

    // metronome servo positioning penduluum

    //new metronome code
    if (motors) {
//      //71 beats in song
//      if (i_note_index == 0) {
//        metronomeTimer = millis();
//        metronomeMovement = 0;
//      }
//      if (i_note_index < 25) {
//        metronomeMovement += 1;
//      } else {
//        metronomeMovement -= 1;
//      }
//      if (metronomeTimer > tempo*100) {
//        Serial.print("Angle: ");
//        Serial.println(metronomeMovement);
//        metronomeServo.write(metronomeMovement);
//        metronomeTimer = millis();
//      }

      //old metronome code
      
      metronomePos = i_note_index;
      if (metronomePos >= 27) {
        metronomePosMapped = map(metronomePos, 28, 53, 100, 0);
      }
      else {
        metronomePosMapped = map(metronomePos, 0, 27, 0, 100);
      }
      //    Serial.print("metronome position: ");
      //    Serial.println(metronomePosMapped);
      metronomeServo.write(metronomePosMapped);

      //Stepper Motor
      int angle = servoNotes[i_note_index];
      int difference = angle - currAngle;
      myStepper.step(difference / degree);
      currAngle = angle;
    }
    //led strip output
    if (lights) {
      strip.clear();
      strip.setPixelColor(ledIndexes[i_note_index], ledColors[i_note_index]);         //  Set pixel's color (in RAM)
      strip.show();
      //    Serial.print("Note playing: ");
      //    Serial.println(notes[i_note_index]);
    }

    long currTime = millis();
    while (millis() - currTime < duration) {
      if (!digitalRead(START_BUTTON)) {
        buttonISR();
        break;
      }
//      //71 beats in song
//      if (i_note_index == 0) {
//        metronomeTimer = millis();
//        metronomeMovement = 0;
//      }
//      if (i_note_index < 25) {
//        metronomeMovement += 1;
//      } else {
//        metronomeMovement -= 1;
//      }
//      if (millis() - metronomeTimer > tempo*1000) {
//        Serial.print("Rest Length: ");
//        Serial.println(tempo*1000);
//        Serial.print("Angle: ");
//        Serial.println(metronomeMovement);
//        metronomeServo.write(metronomeMovement);
//        metronomeTimer = millis();
//      }
    }

    //increment the note counter
    i_note_index += 2; //as delay covers for the rests, we can skip them here
    if (i_note_index >= songLength)
    {
      i_note_index = 0;
      metronomePos = 0;
    }
  }
}
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

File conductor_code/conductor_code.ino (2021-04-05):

//-----------------------------------------------------
// Engineer: Tim Brothers
// Overview
//    When this device is turned on it plays the song Row
//    Row Row Your Boat.
// Design Name:   The Conductor
// File Name:     conductor.c
//
// Inputs:
//		Box Tilt Sensor: Tell the Conductor when the box is opened
//		Volume: controls the volume
//		Tempo: controls the tempo of the song
// Outputs:
//		Servo: Moves the conductor out of the box
//		DC Motor: Waves the conducors baton
//
// History:       4 January 2020 File created
//
//-----------------------------------------------------

#include <Servo.h>
#include <stdio.h>
#include <math.h>

#define TempoCal 512
#define TempoPotMax 1023
#define PwmMax 255

#define rest 0

#define Octive 4

//Music Notes based on Octive--
#define C 16.3516*pow(2,Octive)
#define D 18.35405*pow(2,Octive)
#define E 20.60172*pow(2,Octive)
#define F 21.82676*pow(2,Octive)
#define G 24.49971*pow(2,Octive)
#define A 27.5*pow(2,Octive)
#define B 30.86771*pow(2,Octive)
#define high_C 32.70320*pow(2,Octive)
#define rest 0


#define speakerPIN 5
#define motorPIN 6


//Row Row Row Your Boat
int songLength = 54;
int notes[] = {C, rest, C, rest, C, rest, D, rest, E, rest, E, rest, D, rest, E, rest, F, rest, G, rest, high_C, rest, high_C, rest, high_C, rest, G, rest, G, rest, G, rest, E, rest, E, rest, E, rest, C, rest, C, rest, C, rest, G, rest, F, rest, E, rest, D, rest, C, rest};
int beats[] = {2, 1, 2, 1, 2, 1, 1, 1, 2, 1, 2, 1, 1, 1, 2, 1, 1, 1, 6, 1, 1, 1, 1, 1, 1, 1, 1, 1, 1, 1, 1, 1, 1, 1, 1, 1, 1, 1, 1, 1, 1, 1, 1, 1, 2, 1, 1, 1, 2, 1, 1, 1, 5, 1};

int song_tempo = 250;

//setup the servo output
Servo servo_10;

void setup()
{
  pinMode(A0, INPUT);
  pinMode(A1, INPUT);

  //set up outputs
  pinMode(speakerPIN, OUTPUT);
  pinMode(4, OUTPUT);
  pinMode(7, OUTPUT);
  pinMode(8, OUTPUT);
  pinMode(motorPIN, OUTPUT);

  servo_10.attach(10);

  //set the motor and servo to zero initial condition.
  digitalWrite(motorPIN, 0);
  servo_10.write(0);

  //debug only
  Serial.begin(9600);
  Serial.print("Setup Complete\n");
}

void loop()
{
  int duration;
  int tempo;
  int tempo_pot;
  int motor_speed;
  static const uint8_t analog_pins[] = {A2, A3, A4, A5};


  //------------------------------------
  //while the box is open play the song
  //------------------------------------

  //play the song
  int i_note_index = 0;
  while (1)
  {
    //read the tempo pot
    tempo_pot = analogRead(A0);
    tempo = song_tempo * float(tempo_pot) / TempoCal;	//read the tempo POT
    tempo = 150; // lower numbers = higher speed
    //set the Motor speed
    motor_speed = (1 - float(tempo_pot) / TempoPotMax) * PwmMax;
    analogWrite(motorPIN, motor_speed);

    //play the song
    duration = beats[i_note_index] * tempo;
    tone(speakerPIN, notes[i_note_index], duration);
    delay(duration);

    //increment the note counter
    ++i_note_index;
    if (i_note_index >= songLength)
    {
      i_note_index = 0;
    }
  }

  //When the top of the box is closed
  //Stop the motor
  noTone(motorPIN);

  //move the conductor inside
  servo_10.write(0);

  //Set the LEDs
  digitalWrite(8, LOW);	//turn off the green LED
  digitalWrite(7, HIGH);	//turn on the yellow LED
  delay(1000); // Wait for 1000 millisecond(s)
}

/*
  switch (currentState) {
   case ST_IDLE:
       // do something in the idle state
       break;
    case ST_STOP:
       // do something in the stop state
       break;
    // etc...
  }
*/

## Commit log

2021-02-05 adding arduino files
2021-02-10 Low Pass Filter
2021-02-16 arduino testing code
2021-02-18 adding preliminary output filter + EG schematic
    [clockBot_filterandEG.kicad_pcb, clockBot_filterandEG.sch]
2021-02-18 updated the arduino code. now the servos rotate with the notes and the leds light up with the notes. also the metronome servo works too
2021-03-01 adding clock face 3d file
    [clockBot_filterandEG.sch]
2021-03-05 Stepper Motor
2021-03-05 Stepper motor update
2021-03-05 Stepper Motor updated
2021-03-05 changed stepper motor code to work with 1.8 degree motor
2021-03-09 clockbot user interface
    [clockBot_userInterface.sch]
2021-03-09 rearranged schematic and pcb folders to be easier to navigate
    [clockBot_filterandEG.kicad_pcb, clockBot_filterandEG.sch, clockBot_userInterface.sch]
2021-03-09 Interface update
    [clockBot_userInterface.sch]
2021-03-10 organized folders and added erin grace schematic
    [Juniordesignfilterandenvelopecircuitschematic.sch, clockBot_userInterface.sch]
2021-03-10 User interface update
    [clockBot_userInterface.sch]
2021-03-10 Updated user interface
    [clockBot_userInterface.sch]
2021-03-11 main board schematic done
2021-03-11 8pin molex user interface
    [clockBot_userInterface.sch]
2021-03-11 PCB Board
    [clockBot_userInterface.brd]
2021-03-12 User interface PCB update
    [clockBot_userInterface.brd]
2021-03-12 Fixed switch on user interface
    [clockBot_userInterface.brd, clockBot_userInterface.sch]
2021-03-12 User itnerface switch update
    [clockBot_userInterface.brd, clockBot_userInterface.sch]
2021-03-12 clockface svg file for laser cut
    [Juniordesignfilterandenvelopecircuitschematic.brd]
2021-03-12 main board pcb initial layout
    [Juniordesignfilterandenvelopecircuitschematic.sch]
2021-03-12 updated main pcb
    [pre_autoRoute.brd, pre_autoRoute.sch]
2021-03-12 User interface single row molex
    [clockBot_userInterface.brd, clockBot_userInterface.sch]
2021-03-12 User interface labels
    [clockBot_userInterface.brd]
2021-03-13 Finalized board
    Changed labels and performed a design rule check.
    [Finalized Eagle Board Junior Design.brd]
2021-03-13 finalized PCBs and exported gerbers
    [clockBot_userInterface.brd, clockBot_userInterface.sch, mainBoard_Bom.csv]
2021-03-16 Small fixes (syntax errors & var definitions)
    [ece3872_clockBot_arduino_2.ino]
2021-03-19 updated new clock face with the finalized pcb
    [Finalized Eagle Board Junior Design.dxf]
2021-03-29 Test mode fix 2
    [ece3872_clockBot_arduino_2.ino]
2021-03-31 Reintigrating processing code w/ button press
2021-04-02 laser cut svg files added
    [clockBot_userInterface.dxf]
2021-04-02 Added LEDs for play/test and octave select
2021-04-02 LED test/play fix
2021-04-07 updating svgs
    [Servo, Metal Gear, MG90S.SLDPRT, Servo, Metal Gear, MG90S.STEP, Servo, Metal Gear, MG90S.STL]
2021-04-07 Stepper motor integrated into Main code
2021-04-07 Added Stepper motor to octave select and test mode
2021-04-07 Extra closing bracket ruined everything
2021-04-09 Removing Delay and Print statements
2021-04-09 Fix for metronome code
    [ece3872_clockBot_arduino_2.ino]
2021-04-09 Fixed input test LEDS
    [ece3872_clockBot_arduino_2.ino]
2021-04-09 Stepper motor auto change after octave select
2021-04-09 Stepper motor auto change after octave select (2)
2021-04-09 Stepper Motor Stuff
